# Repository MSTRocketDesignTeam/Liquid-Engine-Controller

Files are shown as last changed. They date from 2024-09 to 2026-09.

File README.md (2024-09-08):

<p align="center">
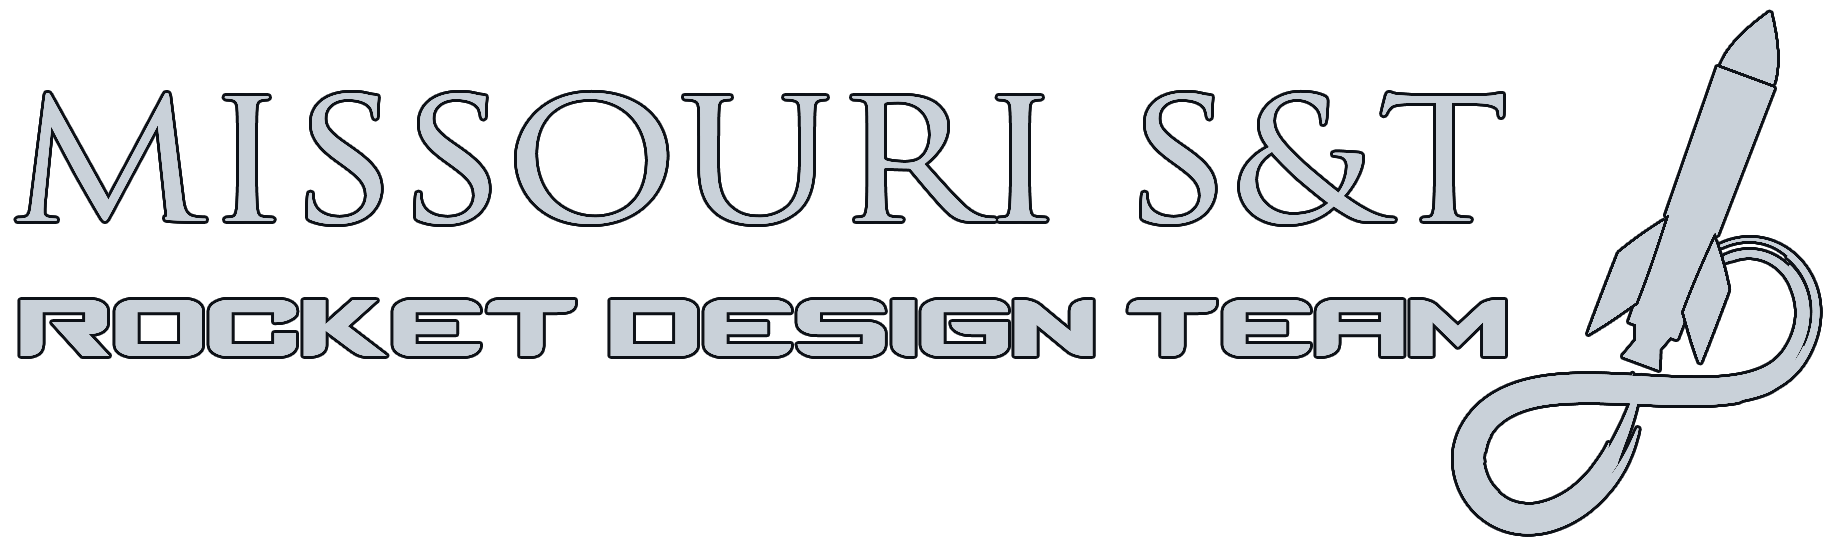
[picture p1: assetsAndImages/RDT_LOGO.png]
Missouri S&T Rocket Design Team
    
</p>

<p align="center"><sup><em>*This repo is intended for educational purposes only*</em></sup></p>

# SRAD Engine Controller
A student researched and designed (SRAD) engine controller for the liquid bipropellant rocket. 

## About
This project is the first iteration of the flight controller for the Rocket Design Team's (RDT) liquid bipropellant rocket.
It aims to provide basic engine control functionality, such as opening and closing of the servo ball valves (SBV), as well as to set the hardware baseline for more advanced control functionality like throttling algorithms for flight efficiency. Additionally, the Liquid Engine Controller (LEC) aims to serve as the data acquisition computer for the propulsion system, in order to analyze the performance of the propulsion system. 

## Documentation
*placeholder*

## Development 
*placeholder* 

## File Structure
This repo contains three main sections, hardware, firmware, and software.

### Hardware:
The hardware directory will contain all of the files related to the design and assembly of the PCBs. This includes KiCad projects as well as BOMs. 

### Firmware:
The firmware directory will contain all of the code (C++) necessary to operate the above hardware. Once the boards have been designed and assembled this is where significant effort will be made.

### Software: 
The software directory will contain the code (Python) for the LEC's computer interface. This program will be responsible for configuring the LEC prior to launch as well as for displaying live propulsion system state data from the launch pad. 

Future developments may allow for preflight simulations (FEA / CFD of engine, estimated throttling curve, etc.).

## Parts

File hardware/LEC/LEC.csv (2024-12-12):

Source: | C:\Users\Raksh\OneDrive\Desktop\Rocket_Repos\LEC\LEC_Attempts\Liquid-Engine-Controller\hardware\LEC\LEC.kicad_sch
Date: | 12/12/2024 8:57:48 AM
Tool: | Eeschema 7.0.8
Generator: | C:\Program Files\KiCad\7.0\bin\scripting\plugins/bom_csv_grouped_by_value.py
Component Count: | 66
Collated Components:
Item | Qty | Reference(s) | Value | LibPart | Footprint | Datasheet | DNP | DigiKey | MANUFACTURER | MAXIMUM_PACKAGE_HEIGHT | PARTREV | STANDARD
1 | 11 | C1, C2, C4, C5, C6, C7, C8, C9, C15, C16, C17 | 100n | Device:C | Capacitor_SMD:C_1206_3216Metric | ~ |  | https://www.digikey.com/en/products/detail/murata-electronics/GRM3195C1H104JA05D/13531811
2 | 3 | C3, C10, C11 | 100n | Device:C | Capacitor_SMD:C_0603_1608Metric | https://mm.digikey.com/Volume0/opasdata/d220001/medias/docus/609/CL10B104KB8NNNC_Spec.pdf |  | https://www.digikey.com/en/products/detail/samsung-electro-mechanics/CL10B104KB8NNNC/3886658
3 | 10 | C12, C13, C14, C18, C19, C20, C21, C22, C24, C25 | 10u | Device:C | Capacitor_SMD:C_0805_2012Metric | https://mm.digikey.com/Volume0/opasdata/d220001/medias/docus/5545/CL21A106KAYNNNE%20Spec.pdf |  | https://www.digikey.com/en/products/detail/samsung-electro-mechanics/CL21A106KAYNNNE/3888549
4 | 2 | C23, C26 | 10n | Device:C | Capacitor_SMD:C_0603_1608Metric | https://search.murata.co.jp/Ceramy/image/img/A01X/G101/ENG/GRM1885C1H103JA01-01.pdf |  | https://www.digikey.com/en/products/detail/murata-electronics/GRM1885C1H103JA01D/4421555
5 | 1 | D1 | 1N5817 | Diode:1N5817 | Diode_THT:D_DO-41_SOD81_P10.16mm_Horizontal | http://www.vishay.com/docs/88525/1n5817.pdf |  | https://www.digikey.com/en/products/detail/vishay-general-semiconductor-diodes-division/1N5817-E3-73/2139978
6 | 12 | J1, J2, J3, J4, J5, J6, J7, J8, J11, J12, J13, J14 | 54-00278 | 4_Pin_M8_Socket_Female:54-00278 | M8Connector:TENSILITY_54-00278 | https://tensility.s3.us-west-2.amazonaws.com/uploads/pdffiles/54-00278.pdf |  | https://www.digikey.com/en/products/detail/tensility-international-corp/54-00278/16604875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 | Tensility | 20.2 mm | A | Manufacturer Recommendations
7 | 2 | J9, J10 | Conn_01x02 | Connector_Generic:Conn_01x02 | Connector_AMASS:AMASS_XT30UPB-M_1x02_P5.0mm_Vertical | ~
8 | 16 | R1, R2, R3, R4, R5, R6, R7, R8, R9, R10, R11, R12, R13, R14, R15, R16 | 10K | Device:R_US | Resistor_SMD:R_0603_1608Metric | ~ |  | https://www.digikey.com/en/products/detail/vishay-dale/TNPW060310K0BEEA/1606881
9 | 1 | U1 | Pico | RaspberryPiPico:Pico | RPiPico:RPi_Pico_SMD_TH | https://datasheets.raspberrypi.com/pico/pico-datasheet.pdf |  | https://www.digikey.com/en/products/detail/raspberry-pi/SC0917/16608257
10 | 1 | U2 | L7805 | Regulator_Linear:L7805 | L7805CV:TO-220_STM | http://www.st.com/content/ccc/resource/technical/document/datasheet/41/4f/b3/b0/12/d4/47/88/CD00000444.pdf/files/CD00000444.pdf/jcr:content/translations/en.CD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 |  | https://www.digikey.com/en/products/detail/stmicroelectronics/L7805CV/585964
11 | 1 | U3 | MC7809CTG | MC7809CTG:MC7809CTG | MC7809CTG:TO-220AB_ONS | MC7809CTG |  | https://www.digikey.com/en/products/detail/onsemi/MC7809CTG/1481254
12 | 1 | U4 | W25Q128JVSIQ | W25Q128JVSIQ:W25Q128JVSIQ | W25Q128JVSIQ:SOIC_128JVSIQ_WIN | https://www.winbond.com/resource-files/W25Q128JV%20RevI%2008232021%20Plus.pdf |  | https://www.digikey.com/en/products/detail/winbond-electronics/W25Q128JVSIQ/5803943
13 | 2 | U5, U6 | MAX31855KASA | Sensor_Temperature:MAX31855KASA | Package_SO:SOIC-8_3.9x4.9mm_P1.27mm | http://datasheets.maximintegrated.com/en/ds/MAX31855.pdf |  | https://www.digikey.com/en/products/detail/analog-devices-inc-maxim-integrated/MAX31855KASA/2591564
14 | 2 | U7, U8 | L78L33ACZ | L78L33ACZ:L78L33ACZ | L78L33ACZ:TO-92-TR_STM | L78L33ACZ |  | https://www.digikey.com/en/products/detail/stmicroelectronics/L78L33ACZ/1038304
15 | 1 | U15 | MCP3564RT-E/ST | MCP3564:MCP3564RT-E_ST | MCP3564R/T:TSSOP20_ST_MCH | https://ww1.microchip.com/downloads/aemDocuments/documents/APID/ProductDocuments/DataSheets/MCP3561_2_4R-Data-Sheet-DS200006391C.pdf |  | https://www.digikey.com/en/products/detail/microchip-technology/MCP3564RT-E-ST/12807301

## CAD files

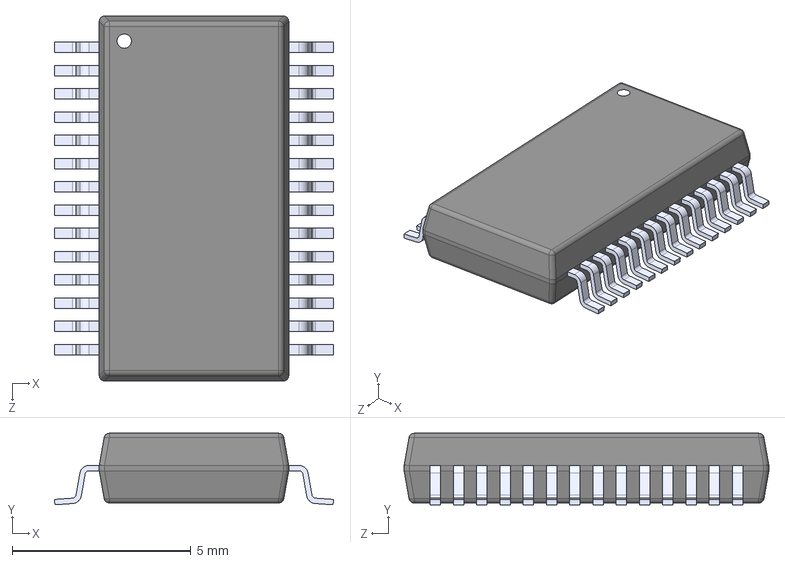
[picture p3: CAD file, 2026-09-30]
hardware/ADC Hat - LEC/components/ADS1256IDBR/ADS1256IDBR.step
7.80 x 2.00 x 10.2 mm

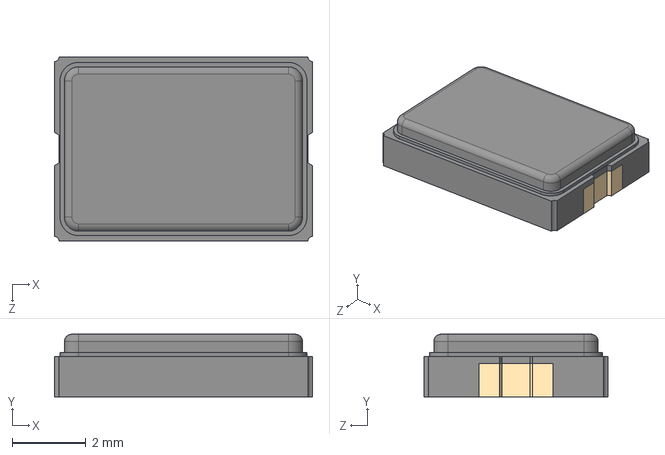
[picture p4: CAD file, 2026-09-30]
hardware/ADC Hat - LEC/components/ECS-100-S-20A-TR/ECS-100-S-20A-TR.step
7.00 x 1.70 x 5.00 mm

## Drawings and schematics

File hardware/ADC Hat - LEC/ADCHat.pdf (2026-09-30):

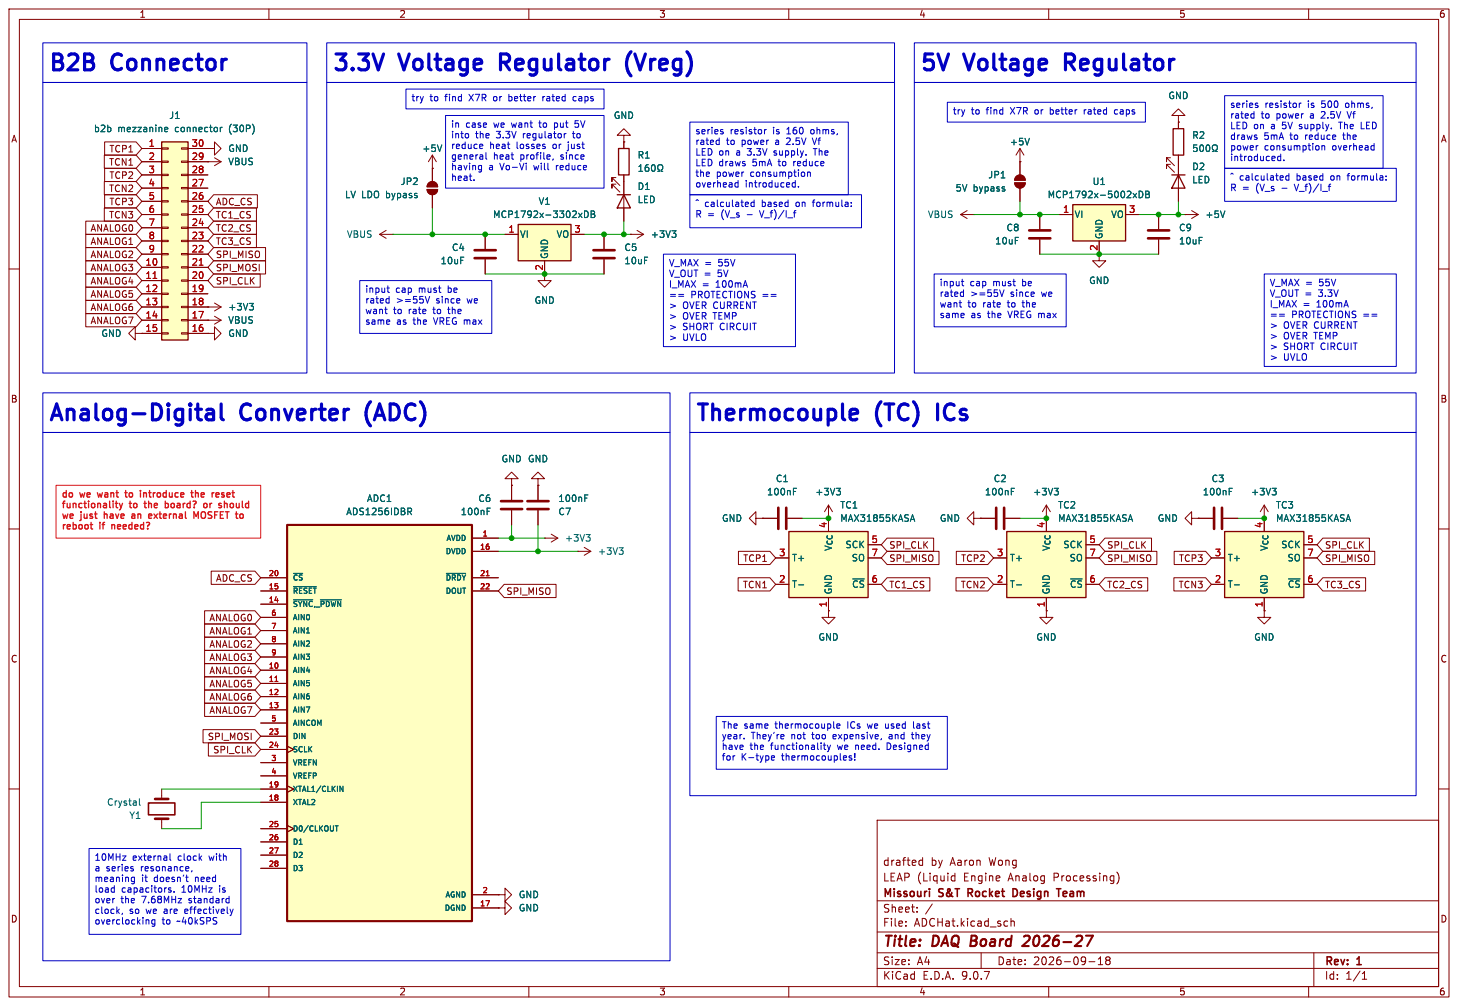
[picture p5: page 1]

https://www.digikey.com/en/products/filter/led-indication-discrete/105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 C6

try to find X7R or better rated caps Thermocouple (TC) ICs

in case we want to put 5V
reduce heat losses or just
having a Vo-Vi will reduce
heat.

draws 5mA to reduce the

LED draws 5mA to reduce
the power consumption
overhead introduced.

input cap must be

same as the VREG max

do we want to introduce the reset

1 SCK 5 SO 7 ~{CS}6 TC3 MAX31855KASA GND GND

1 SCK 5 SO 7 ~{CS}6 GND

1 SCK 5 SO 7 ~{CS}6 GND GND

a series resonance, meaning it doesn't need

clock, so we are effectively

Id: 1/1 Title: DAQ Board 2026-27

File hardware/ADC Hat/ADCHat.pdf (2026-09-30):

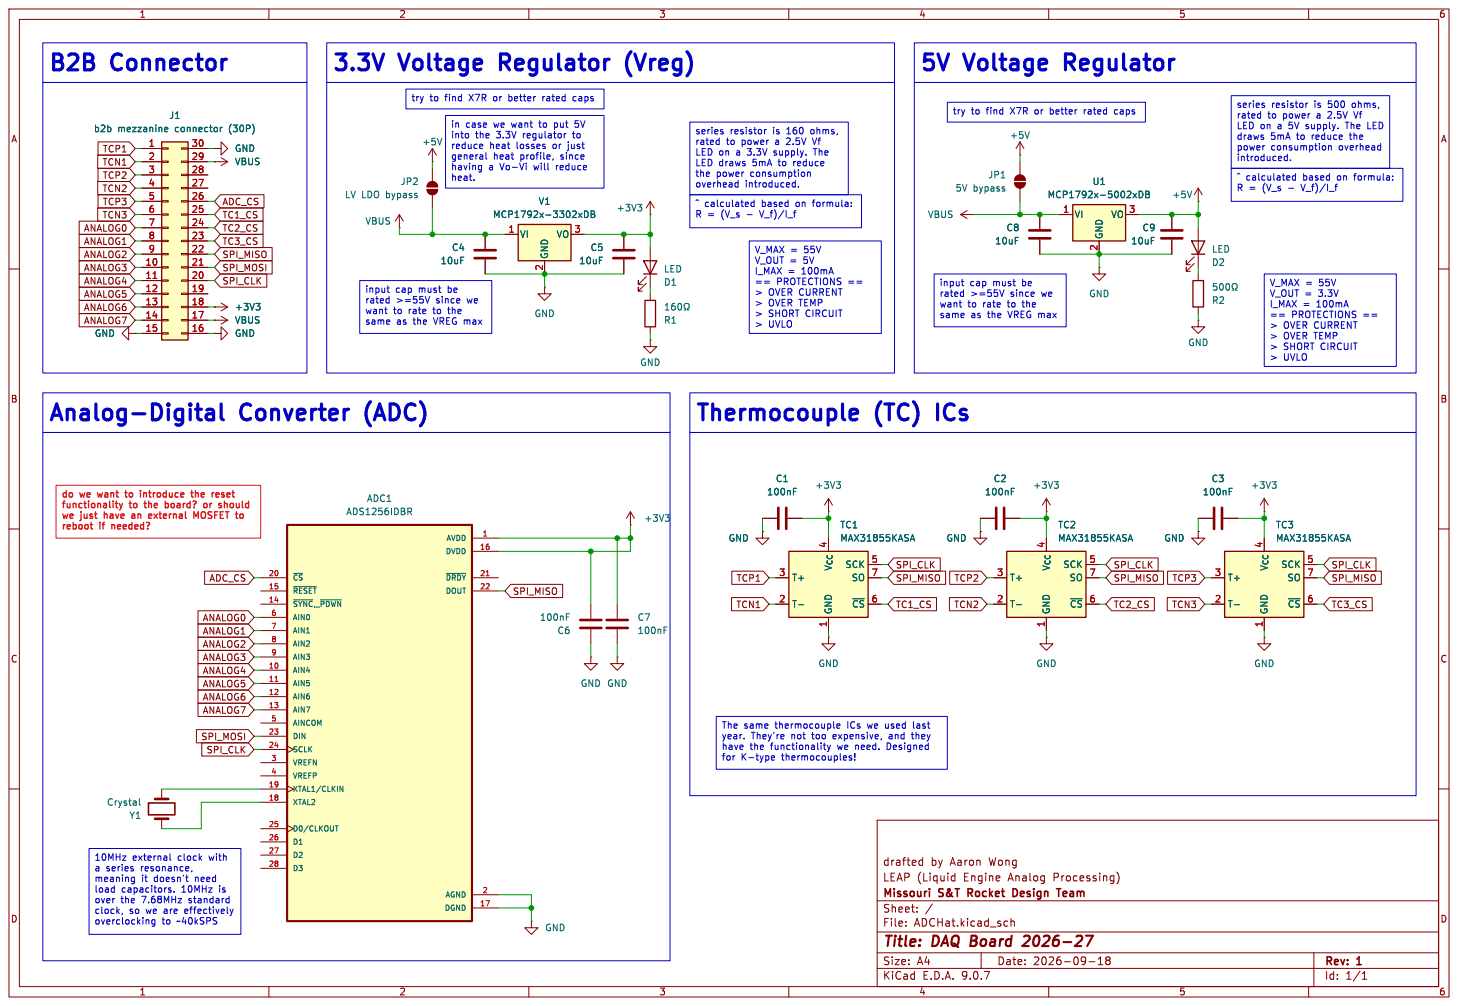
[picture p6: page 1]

https://www.digikey.com/en/products/filter/led-indication-discrete/105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 U1 MCP1792x-5002xDB

same as the VREG max 5V Voltage Regulator

try to find X7R or better rated caps

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

LED draws 5mA to reduce
the power consumption
overhead introduced. Thermocouple (TC) ICs

LV LDO bypass VBUS

input cap must be

1 SCK 5 SO 7 ~{CS}6 TC1 GND MAX31855KASA C1
100nF GND

1 SCK 5 SO 7 ~{CS}6 TC2 MAX31855KASA GND GND

a series resonance, meaning it doesn't need

clock, so we are effectively

Id: 1/1 Title: DAQ Board 2026-27

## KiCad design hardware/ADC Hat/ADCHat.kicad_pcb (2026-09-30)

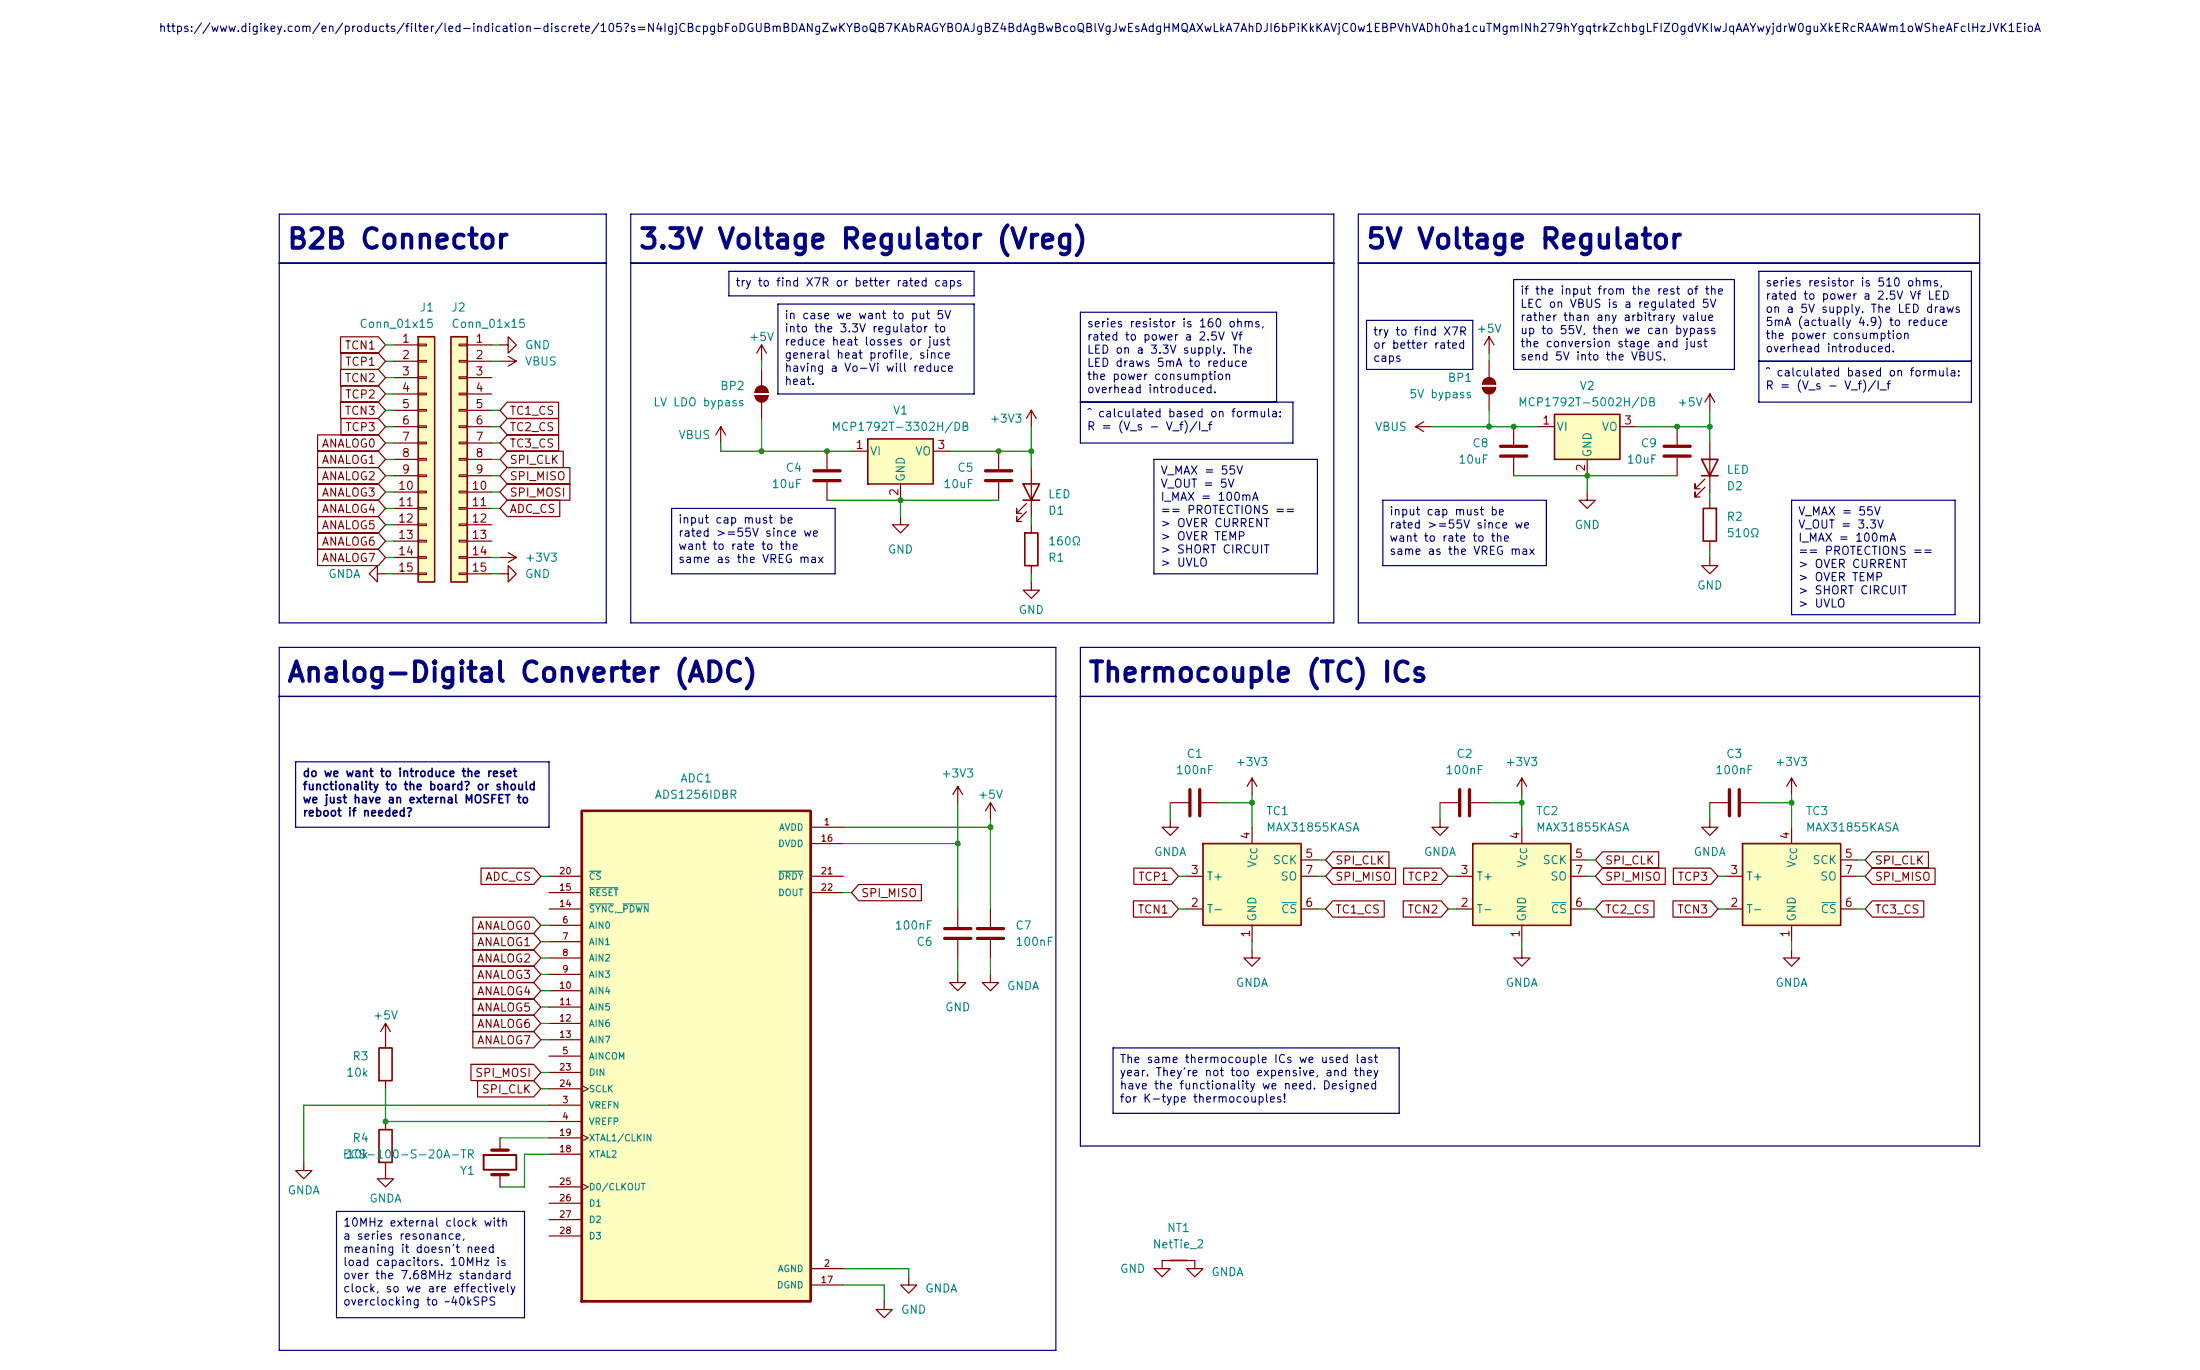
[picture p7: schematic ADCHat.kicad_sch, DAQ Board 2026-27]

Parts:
ADC1: ADS1256IDBR; SOP65P780X200-28N; DIGIKEY_ID ADS1256IDBR
BP1: 5V bypass; SolderJumper-2_P1.3mm_Open_RoundedPad1.0x1.5mm
BP2: LV LDO bypass; SolderJumper-2_P1.3mm_Open_RoundedPad1.0x1.5mm
C1, C2, C3: 100nF; C_0402_1005Metric; DIGIKEY_ID GRM155R71H104KE14D
C4, C8: 10uF; C_0805_2012Metric; DIGIKEY_ID GMC21X5R106K50NT
C5, C9: 10uF; C_0805_2012Metric; DIGIKEY_ID CL21A106KPFNNNG
C6, C7: 100nF; C_0805_2012Metric; DIGIKEY_ID CL21B104KBCNNNC
D1, D2: LED; LED_0603_1608Metric; DIGIKEY_ID KT EELP41.12-S2U1-25-2X4Y-5-R18
J1, J2: Conn_01x15; PinHeader_1x15_P2.54mm_Vertical
NT1: NetTie_2; NetTie-2_SMD_Pad0.5mm
R1: 160Ω; R_0603_1608Metric; DIGIKEY_ID RC0402FR-07160RL
R2: 510Ω; R_0603_1608Metric; DIGIKEY_ID RC0402FR-07510RL
R3, R4: 10k; R_0603_1608Metric; DIGIKEY_ID RNCF0402BTE10K0
TC1, TC2, TC3: MAX31855KASA; SOIC-8_3.9x4.9mm_P1.27mm; DIGIKEY_ID MAX31855KASA+T
V1: MCP1792T-3302H/DB; SOT-223-3_TabPin2; DIGIKEY_ID MCP1792T-3302H/DB
V2: MCP1792T-5002H/DB; SOT-223-3_TabPin2; DIGIKEY_ID MCP1792T-5002H/DB
Y1: ECS-100-S-20A-TR; XTAL_ECS-100-S-20A-TR; DIGIKEY_ID ECS-100-S-20A-TR

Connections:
+3V3: ADC1.16 (DVDD), C1.2, C2.2, C3.2, C5.1, C6.1, D1.2 (A), J2.14, TC1.4 (V_{CC}), TC2.4 (V_{CC}), TC3.4 (V_{CC}), V1.3 (VO)
+5V: ADC1.1 (AVDD), BP1.2 (B), BP2.2 (B), C7.2, C9.1, D2.2 (A), R3.1, V2.3 (VO)
ADC_CS: ADC1.20 (~CS), J2.11
ANALOG0: ADC1.6 (AIN0), J1.7
ANALOG1: ADC1.7 (AIN1), J1.8
ANALOG2: ADC1.8 (AIN2), J1.9
ANALOG3: ADC1.9 (AIN3), J1.10
ANALOG4: ADC1.10 (AIN4), J1.11
ANALOG5: ADC1.11 (AIN5), J1.12
ANALOG6: ADC1.12 (AIN6), J1.13
ANALOG7: ADC1.13 (AIN7), J1.14
GND: ADC1.17 (DGND), C4.2, C5.2, C6.2, C8.2, C9.2, J2.1, J2.15, NT1.1, R1.1, R2.1, V1.2 (GND), V2.2 (GND)
GNDA: ADC1.2 (AGND), ADC1.3 (VREFN), C1.1, C2.1, C3.1, C7.1, J1.15, NT1.2, R4.2, TC1.1 (GND), TC2.1 (GND), TC3.1 (GND)
unnamed: ADC1.4 (VREFP), R3.2, R4.1
unnamed: ADC1.19 (XTAL1/CLKIN), Y1.1
unnamed: ADC1.18 (XTAL2), Y1.2
unnamed: D1.1 (K), R1.2
unnamed: D2.1 (K), R2.2
SPI_CLK: ADC1.24 (SCLK), J2.8, TC1.5 (SCK), TC2.5 (SCK), TC3.5 (SCK)
SPI_MISO: ADC1.22 (DOUT), J2.9, TC1.7 (SO), TC2.7 (SO), TC3.7 (SO)
SPI_MOSI: ADC1.23 (DIN), J2.10
TC1_CS: J2.5, TC1.6 (~CS)
TC2_CS: J2.6, TC2.6 (~CS)
TC3_CS: J2.7, TC3.6 (~CS)
TCN1: J1.1, TC1.2 (T-)
TCN2: J1.3, TC2.2 (T-)
TCN3: J1.5, TC3.2 (T-)
TCP1: J1.2, TC1.3 (T+)
TCP2: J1.4, TC2.3 (T+)
TCP3: J1.6, TC3.3 (T+)
VBUS: BP1.1 (A), BP2.1 (A), C4.1, C8.1, J2.2, V1.1 (VI), V2.1 (VI)

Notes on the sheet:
https://www.digikey.com/en/products/filter/led-indication-discrete/105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
10MHz external clock with a series resonance, meaning it doesn't need load capacitors. 10MHz is over the 7.68MHz standard clock, so we are effectively overclocking to ~40kSPS
in case we want to put 5V into the 3.3V regulator to reduce heat losses or just general heat profile, since having a Vo-Vi will reduce heat.
input cap must be rated >=55V since we want to rate to the same as the VREG max
5V Voltage Regulator
try to find X7R or better rated caps
V_MAX = 55V V_OUT = 5V I_MAX = 100mA == PROTECTIONS == > OVER CURRENT > OVER TEMP > SHORT CIRCUIT > UVLO
^ calculated based on formula: R = (V_s - V_f)/I_f
do we want to introduce the reset functionality to the board? or should we just have an external MOSFET to reboot if needed?
if the input from the rest of the LEC on VBUS is a regulated 5V rather than any arbitrary value up to 55V, then we can bypass the conversion stage and just send 5V into the VBUS.
Analog-Digital Converter (ADC)
The same thermocouple ICs we used last year. They're not too expensive, and they have the functionality we need. Designed for K-type thermocouples!
3.3V Voltage Regulator (Vreg)
V_MAX = 55V V_OUT = 3.3V I_MAX = 100mA == PROTECTIONS == > OVER CURRENT > OVER TEMP > SHORT CIRCUIT > UVLO
series resistor is 160 ohms, rated to power a 2.5V Vf LED on a 3.3V supply. The LED draws 5mA to reduce the power consumption overhead introduced.
series resistor is 510 ohms, rated to power a 2.5V Vf LED on a 5V supply. The LED draws 5mA (actually 4.9) to reduce the power consumption overhead introduced.
Thermocouple (TC) ICs
B2B Connector

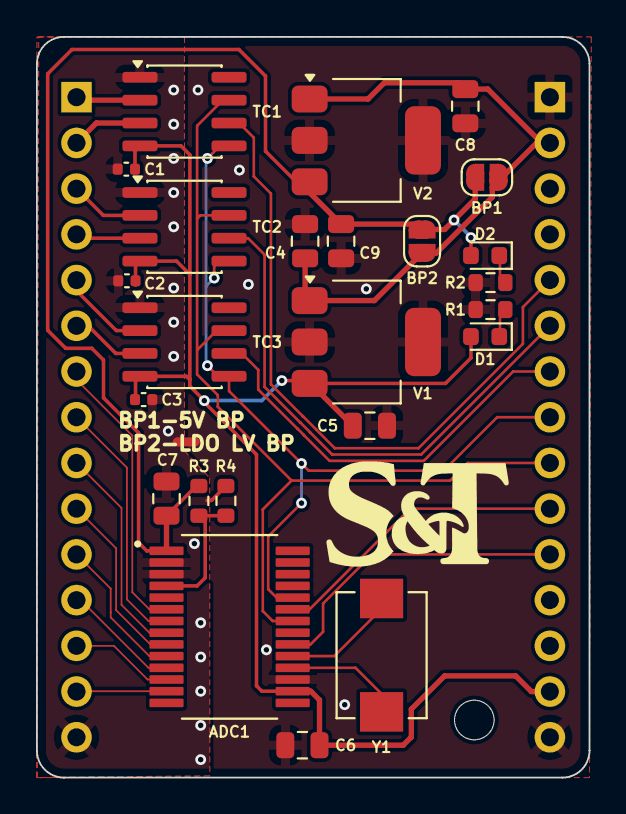
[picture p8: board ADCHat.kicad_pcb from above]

Board: 2 copper layers, 30.7 x 41.1 mm, 27 parts (0 on the bottom side), 31 nets.

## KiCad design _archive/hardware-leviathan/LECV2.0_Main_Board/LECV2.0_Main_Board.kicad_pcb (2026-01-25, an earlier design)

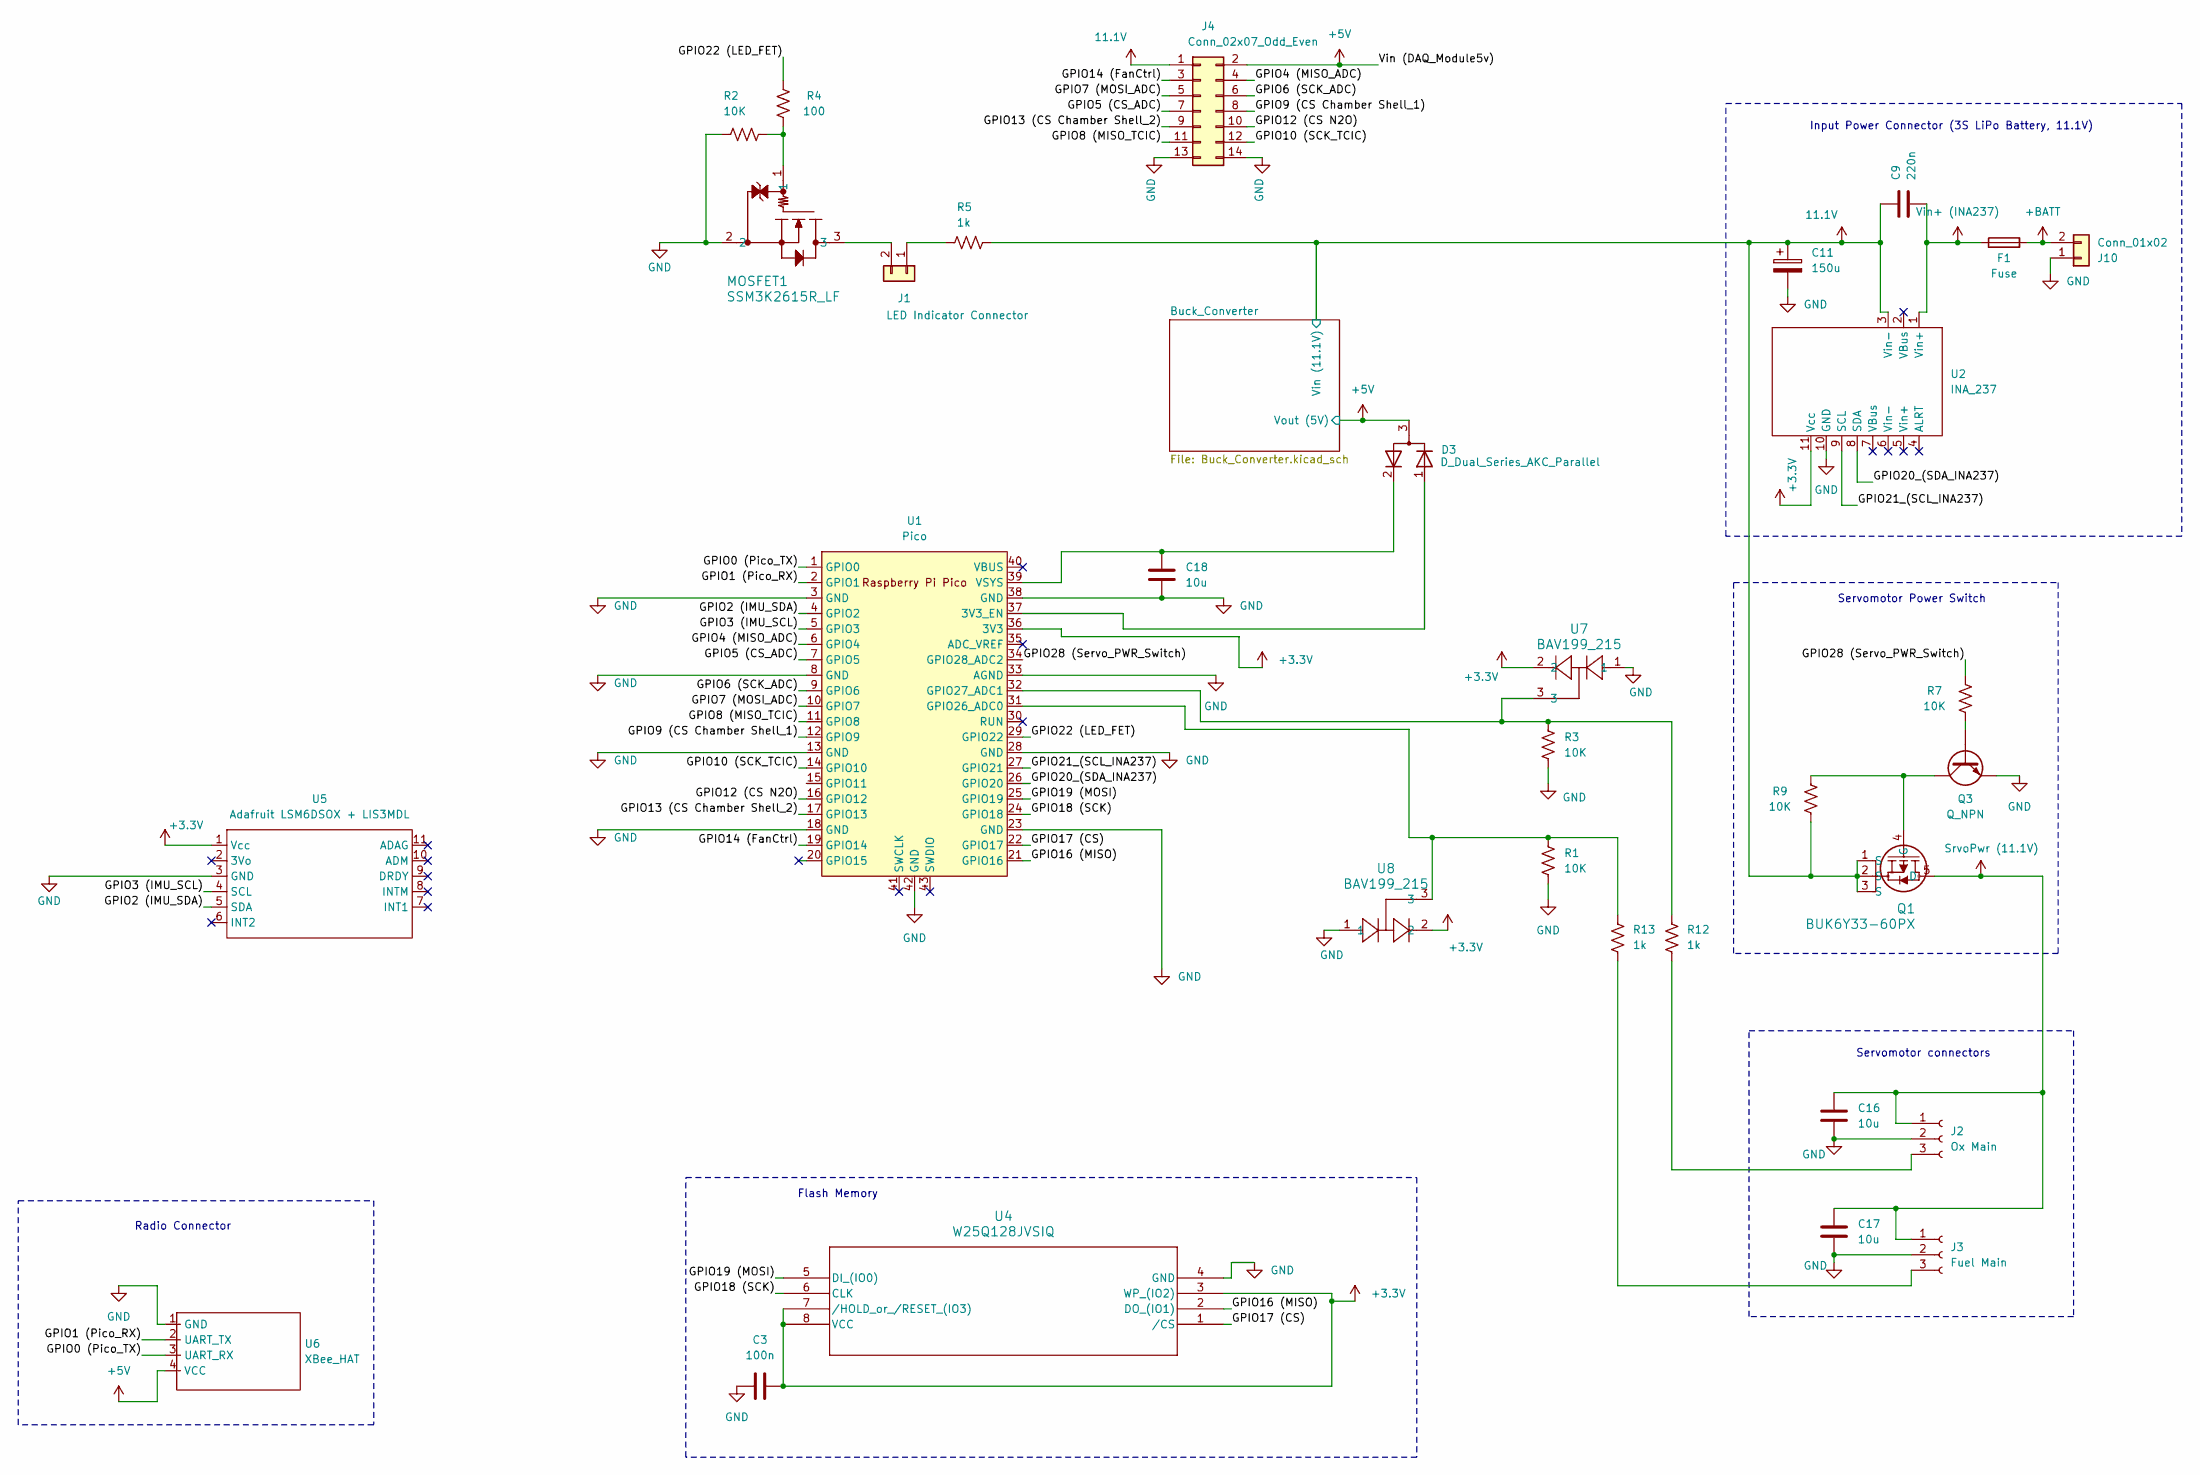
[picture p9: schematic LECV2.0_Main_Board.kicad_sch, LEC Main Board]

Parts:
C3: 100n; C_0603_1608Metric
C9: 220n; C_0805_2012Metric
C11: 150u; CAPPRD500W60D1000H1600
C16, C17, C18: 10u; C_1210_3225Metric
D3: D_Dual_Series_AKC_Parallel; SOT-23
F1: Fuse; Fuse_1206_3216Metric
J1: LED Indicator Connector; PinHeader_1x02_P2.54mm_Vertical
J2: Ox Main; TENSILITY_54-00440
J3: Fuel Main; TENSILITY_54-00440
J4: Conn_02x07_Odd_Even; PinHeader_2x07_P2.54mm_Vertical
J10: Conn_01x02; AMASS_XT30UPB-M_1x02_P5.0mm_Vertical
MOSFET1: SSM3K2615R_LF; SOT-23F_TOS
Q1: BUK6Y33-60PX; LFPAK_SOT669_NEX
Q3: Q_NPN; SOT-323_SC-70
R1, R2, R3, R7, R9: 10K; R_0603_1608Metric
R4: 100; R_0603_1608Metric
R5, R12, R13: 1k; R_0603_1608Metric
U1: Pico; RPi_Pico_SMD_TH
U2: INA_237; INA238_MODULE
U4: W25Q128JVSIQ; SOIC_128JVSIQ_WIN
U5: Adafruit LSM6DSOX + LIS3MDL; Adafruit_LSM6DSOX+LIS3MDL
U6: XBee_HAT; XBee-HAT
U7, U8: BAV199_215; SOT-23-3

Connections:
11.1V: C9.1, C11.1, J4.1, Q1.1 (S), Q1.2 (S), Q1.3 (S), R5.2, R9.1, U2.3 (Vin-); also elsewhere on the board
+3.3V: C3.2, U1.36 (3V3), U2.11 (Vcc), U4.3 (WP_(IO2)), U4.7 (/HOLD_or_/RESET_(IO3)), U4.8 (VCC), U5.1 (Vcc), U7.2, U8.2
+5V: D3.3 (common), J4.2, U6.4 (VCC); also elsewhere on the board
+BATT: F1.2, J10.2
/GPIO0 (Pico_TX): U1.1 (GPIO0), U6.3 (UART_RX)
/GPIO1 (Pico_RX): U1.2 (GPIO1), U6.2 (UART_TX)
/GPIO2 (IMU_SDA): U1.4 (GPIO2), U5.5 (SDA)
/GPIO3 (IMU_SCL): U1.5 (GPIO3), U5.4 (SCL)
/GPIO4 (MISO_ADC): J4.4, U1.6 (GPIO4)
/GPIO5 (CS_ADC): J4.7, U1.7 (GPIO5)
/GPIO6 (SCK_ADC): J4.6, U1.9 (GPIO6)
/GPIO7 (MOSI_ADC): J4.5, U1.10 (GPIO7)
/GPIO8 (MISO_TCIC): J4.11, U1.11 (GPIO8)
/GPIO9 (CS Chamber Shell_1): J4.8, U1.12 (GPIO9)
/GPIO10 (SCK_TCIC): J4.12, U1.14 (GPIO10)
/GPIO12 (CS N2O): J4.10, U1.16 (GPIO12)
/GPIO13 (CS Chamber Shell_2): J4.9, U1.17 (GPIO13)
/GPIO14 (FanCtrl): J4.3, U1.19 (GPIO14)
/GPIO16 (MISO): U1.21 (GPIO16), U4.2 (DO_(IO1))
/GPIO17 (CS): U1.22 (GPIO17), U4.1 (/CS)
/GPIO18 (SCK): U1.24 (GPIO18), U4.6 (CLK)
/GPIO19 (MOSI): U1.25 (GPIO19), U4.5 (DI_(IO0))
/GPIO20_(SDA_INA237): U1.26 (GPIO20), U2.8 (SDA)
/GPIO21_(SCL_INA237): U1.27 (GPIO21), U2.9 (SCL)
/GPIO22 (LED_FET): R4.1, U1.29 (GPIO22)
/GPIO28 (Servo_PWR_Switch): R7.2, U1.34 (GPIO28_ADC2)
GND: C3.1, C11.2, C16.2, C17.2, C18.2, J2.2, J3.2, J4.13, J4.14, J10.1, MOSFET1.2, Q3.2 (E), R1.2, R2.2, R3.2, U1.3 (GND), U1.8 (GND), U1.13 (GND), U1.18 (GND), U1.23 (GND), U1.28 (GND), U1.33 (AGND), U1.38 (GND), U1.42 (GND), U2.10 (GND), U4.4 (GND), U5.3 (GND), U6.1 (GND), U7.1, U8.1; also elsewhere on the board
unnamed: D3.1 (A), U1.37 (3V3_EN)
unnamed: C18.1, D3.2 (K), U1.39 (VSYS)
unnamed: J1.1, R5.1
unnamed: J1.2, MOSFET1.3
unnamed: J2.3, R12.2
unnamed: J3.3, R13.2
unnamed: MOSFET1.1, R2.1, R4.2
unnamed: Q1.4 (G), Q3.3 (C), R9.2
unnamed: Q3.1 (B), R7.1
unnamed: R1.1, R13.1, U1.31 (GPIO26_ADC0), U8.3
unnamed: R3.1, R12.1, U1.32 (GPIO27_ADC1), U7.3
SrvoPwr (11.1V): C16.1, C17.1, J2.1, J3.1, Q1.5 (D)
Vin+ (INA237): C9.2, F1.1, U2.1 (Vin+)

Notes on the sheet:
Flash Memory
Radio Connector
Servomotor Power Switch
Input Power Connector (3S LiPo Battery, 11.1V)
Servomotor connectors

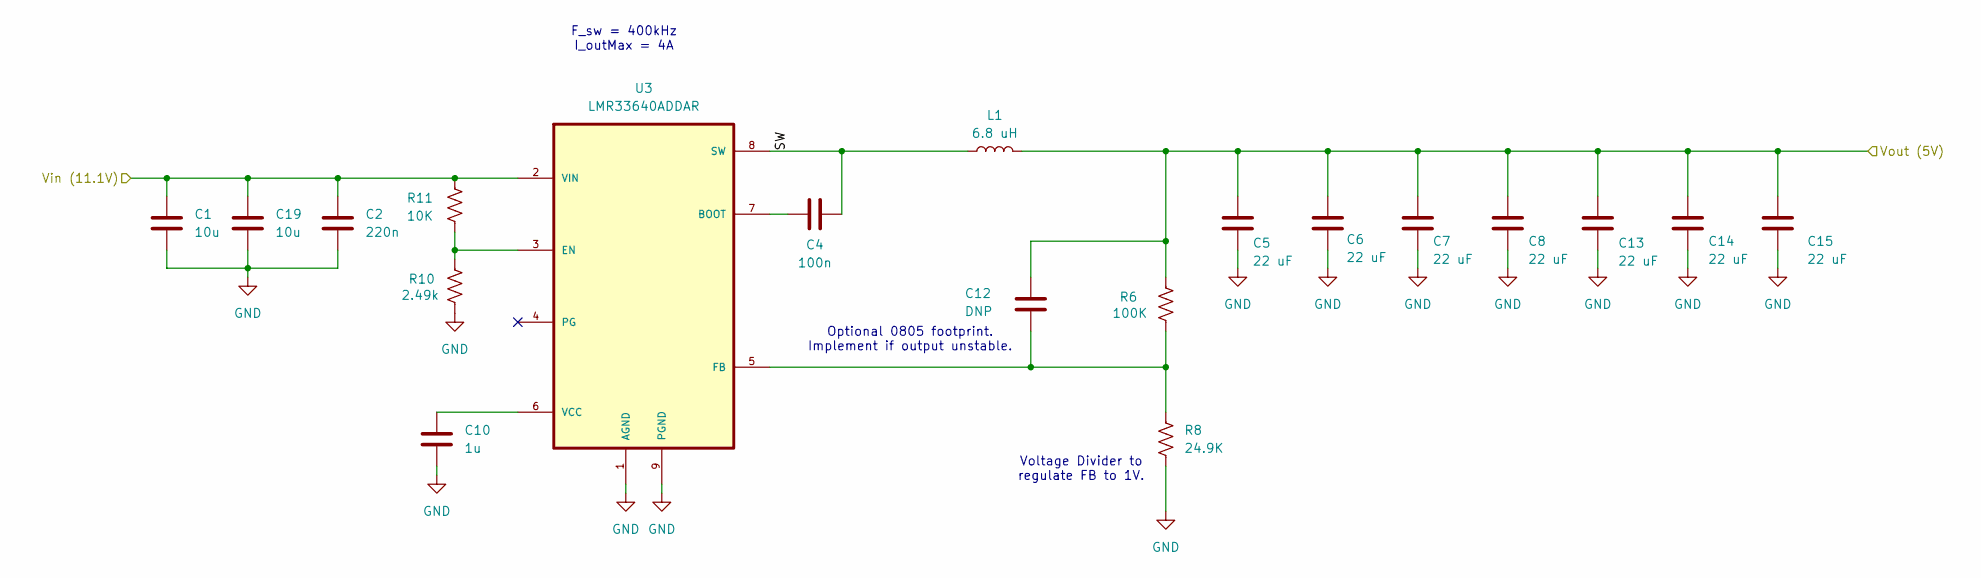
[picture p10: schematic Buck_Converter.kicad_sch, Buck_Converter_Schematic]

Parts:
C1, C19: 10u; C_1210_3225Metric
C2: 220n; C_0805_2012Metric
C4: 100n; C_0603_1608Metric
C5, C6, C7, C8, C13, C14, C15: 22 uF; C_0805_2012Metric
C10: 1u; C_0805_2012Metric
C12: DNP; C_0805_2012Metric
L1: 6.8 uH; IND_CSBX0650-6R8M
R6: 100K; R_0603_1608Metric
R8: 24.9K; R_0603_1608Metric
R10: 2.49k; R_0603_1608Metric
R11: 10K; R_0603_1608Metric
U3: LMR33640ADDAR; Texas_HSOP-8-1EP_3.9x4.9mm_P1.27mm_ThermalVias

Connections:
11.1V: C1.1, C2.1, C19.1, R11.1, U3.2 (VIN); also elsewhere on the board
+5V: C5.1, C6.1, C7.1, C8.1, C12.2, C13.1, C14.1, C15.1, L1.2, R6.2; also elsewhere on the board
/Buck_Converter/SW: C4.2, L1.1, U3.8 (SW)
GND: C1.2, C2.2, C5.2, C6.2, C7.2, C8.2, C10.2, C13.2, C14.2, C15.2, C19.2, R8.2, R10.1, U3.1 (AGND), U3.9 (PGND); also elsewhere on the board
unnamed: C4.1, U3.7 (BOOT)
unnamed: R10.2, R11.2, U3.3 (EN)
unnamed: C12.1, R6.1, R8.1, U3.5 (FB)
unnamed: C10.1, U3.6 (VCC)

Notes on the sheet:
Optional 0805 footprint. Implement if output unstable.
Voltage Divider to regulate FB to 1V.
F_sw = 400kHz I_outMax = 4A

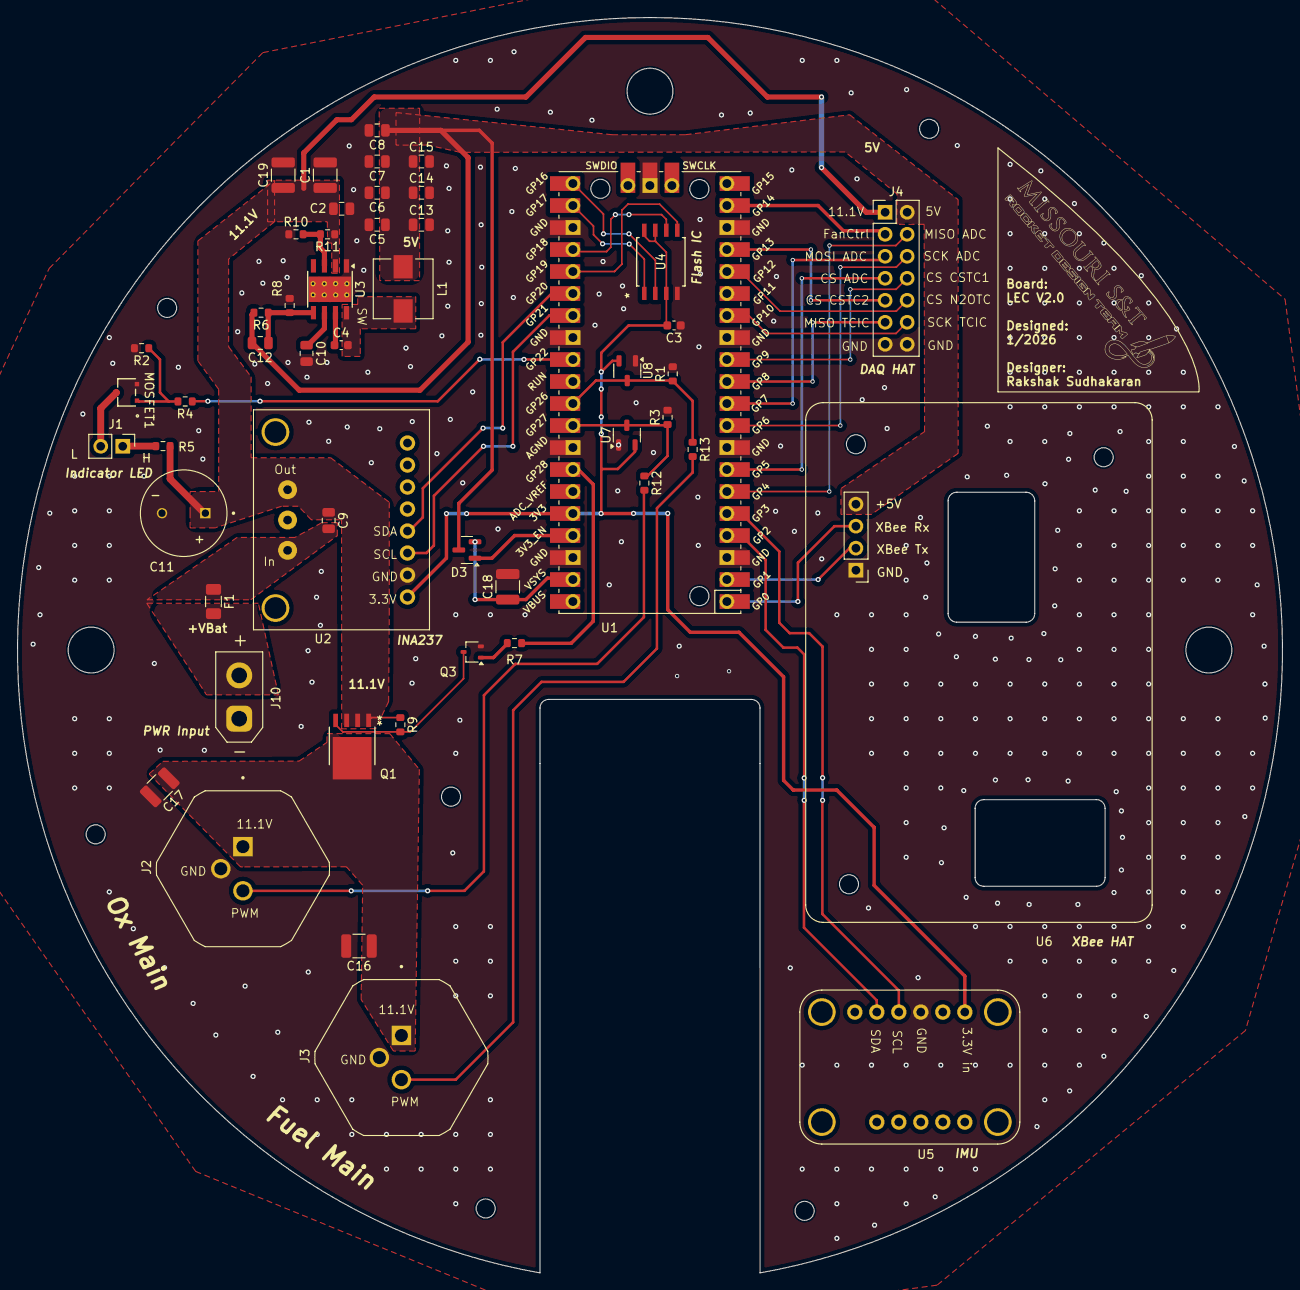
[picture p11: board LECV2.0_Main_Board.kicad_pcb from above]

Board: 2 copper layers, 146.0 x 144.9 mm, 51 parts (0 on the bottom side), 45 nets.

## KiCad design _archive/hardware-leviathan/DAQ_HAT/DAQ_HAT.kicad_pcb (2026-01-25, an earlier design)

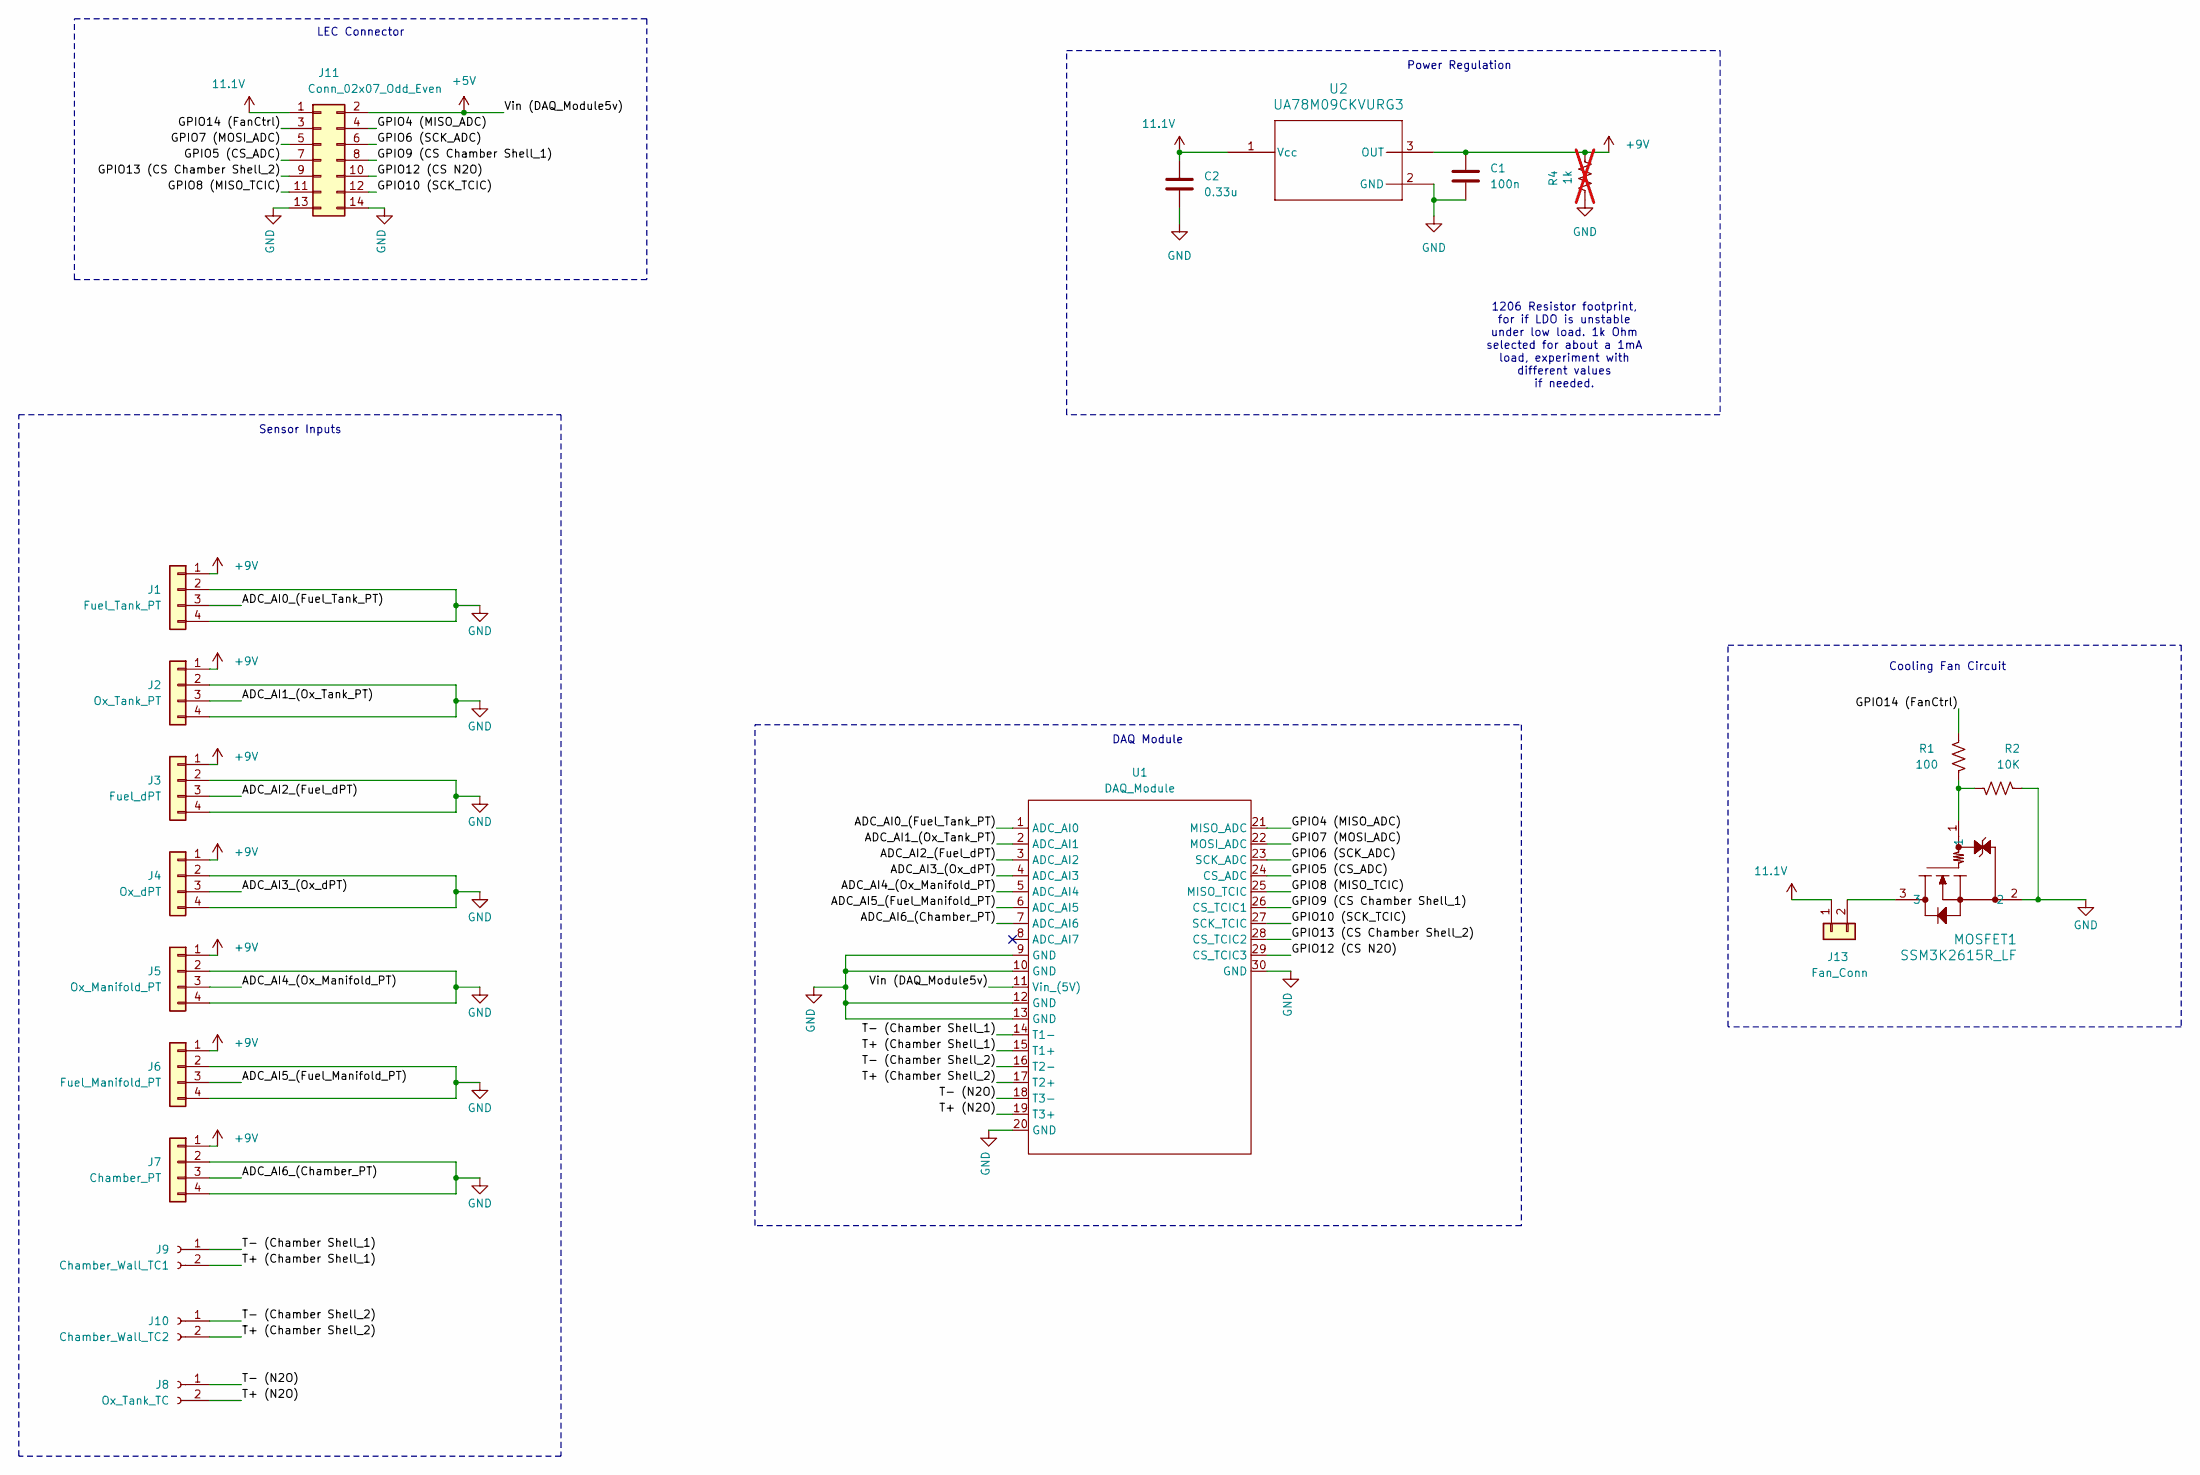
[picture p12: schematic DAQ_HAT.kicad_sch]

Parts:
C1: 100n; C_0603_1608Metric
C2: 0.33u; C_1206_3216Metric
J1: Fuel_Tank_PT; TENSILITY_54-00278
J2: Ox_Tank_PT; TENSILITY_54-00278
J3: Fuel_dPT; TENSILITY_54-00278
J4: Ox_dPT; TENSILITY_54-00278
J5: Ox_Manifold_PT; TENSILITY_54-00278
J6: Fuel_Manifold_PT; TENSILITY_54-00278
J7: Chamber_PT; TENSILITY_54-00278
J8: Ox_Tank_TC; PinHeader_1x02_P2.54mm_Vertical
J9: Chamber_Wall_TC1; PinHeader_1x02_P2.54mm_Vertical
J10: Chamber_Wall_TC2; PinHeader_1x02_P2.54mm_Vertical
J11: Conn_02x07_Odd_Even; PinHeader_2x07_P2.54mm_Vertical
J13: Fan_Conn; PinHeader_1x02_P2.54mm_Vertical
MOSFET1: SSM3K2615R_LF; SOT-23F_TOS
R1: 100; R_0603_1608Metric
R2: 10K; R_0603_1608Metric
R4: 1k; R_1206_3216Metric; not fitted
U1: DAQ_Module
U2: UA78M09CKVURG3; TO-252-2

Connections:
11.1V: C2.2, J11.1, J13.1, U2.1 (Vcc)
+5V: J11.2, U1.11 (Vin_(5V))
+9V: C1.2, J1.1, J2.1, J3.1, J4.1, J5.1, J6.1, J7.1, R4.1, U2.3 (OUT)
/ADC_AI0_(Fuel_Tank_PT): J1.3, U1.1 (ADC_AI0)
/ADC_AI1_(Ox_Tank_PT): J2.3, U1.2 (ADC_AI1)
/ADC_AI2_(Fuel_dPT): J3.3, U1.3 (ADC_AI2)
/ADC_AI3_(Ox_dPT): J4.3, U1.4 (ADC_AI3)
/ADC_AI4_(Ox_Manifold_PT): J5.3, U1.5 (ADC_AI4)
/ADC_AI5_(Fuel_Manifold_PT): J6.3, U1.6 (ADC_AI5)
/ADC_AI6_(Chamber_PT): J7.3, U1.7 (ADC_AI6)
/GPIO4 (MISO_ADC): J11.4, U1.21 (MISO_ADC)
/GPIO5 (CS_ADC): J11.7, U1.24 (CS_ADC)
/GPIO6 (SCK_ADC): J11.6, U1.23 (SCK_ADC)
/GPIO7 (MOSI_ADC): J11.5, U1.22 (MOSI_ADC)
/GPIO8 (MISO_TCIC): J11.11, U1.25 (MISO_TCIC)
/GPIO9 (CS Chamber Shell_1): J11.8, U1.26 (CS_TCIC1)
/GPIO10 (SCK_TCIC): J11.12, U1.27 (SCK_TCIC)
/GPIO12 (CS N2O): J11.10, U1.29 (CS_TCIC3)
/GPIO13 (CS Chamber Shell_2): J11.9, U1.28 (CS_TCIC2)
/GPIO14 (FanCtrl): J11.3, R1.1
/T+ (Chamber Shell_1): J9.2, U1.15 (T1+)
/T+ (Chamber Shell_2): J10.2, U1.17 (T2+)
/T+ (N2O): J8.2, U1.19 (T3+)
/T- (Chamber Shell_1): J9.1, U1.14 (T1-)
/T- (Chamber Shell_2): J10.1, U1.16 (T2-)
/T- (N2O): J8.1, U1.18 (T3-)
GND: C1.1, C2.1, J1.2, J1.4, J2.2, J2.4, J3.2, J3.4, J4.2, J4.4, J5.2, J5.4, J6.2, J6.4, J7.2, J7.4, J11.13, J11.14, MOSFET1.2, R2.2, R4.2, U1.9 (GND), U1.10 (GND), U1.12 (GND), U1.13 (GND), U1.20 (GND), U1.30 (GND), U2.2 (GND)
unnamed: J13.2, MOSFET1.3
unnamed: MOSFET1.1, R1.2, R2.1

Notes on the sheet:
Cooling Fan Circuit
LEC Connector
Sensor Inputs
Power Regulation
DAQ Module
1206 Resistor footprint, for if LDO is unstable under low load. 1k Ohm selected for about a 1mA load, experiment with different values if needed.

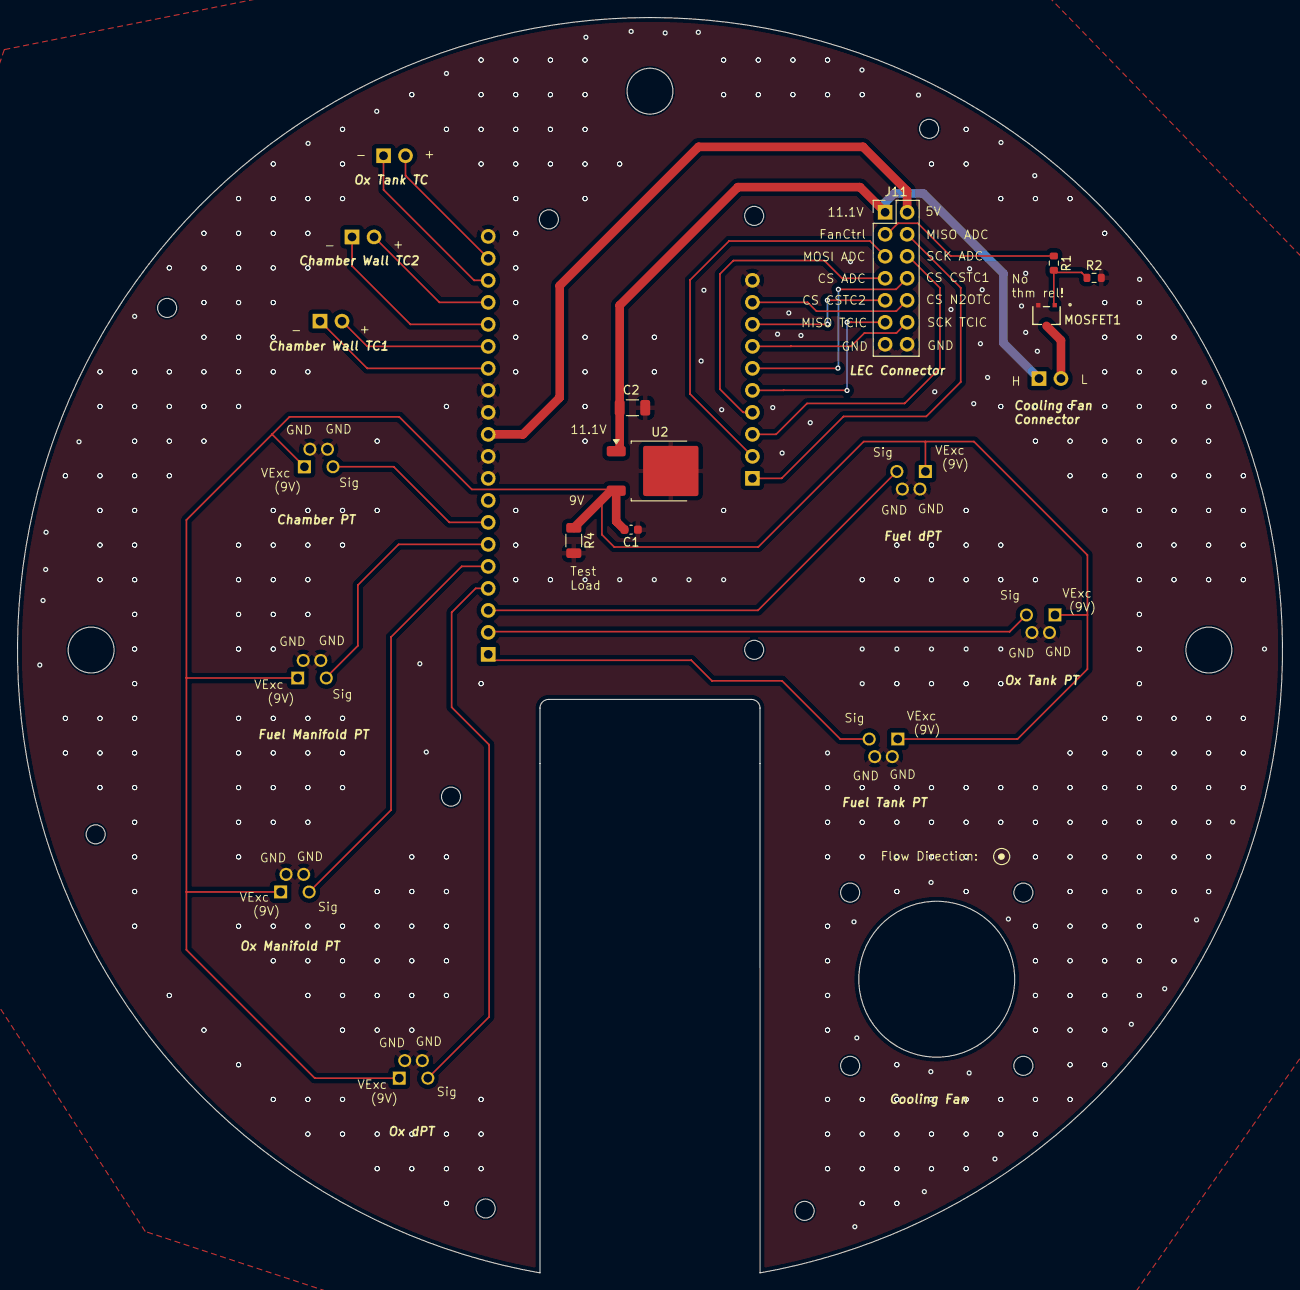
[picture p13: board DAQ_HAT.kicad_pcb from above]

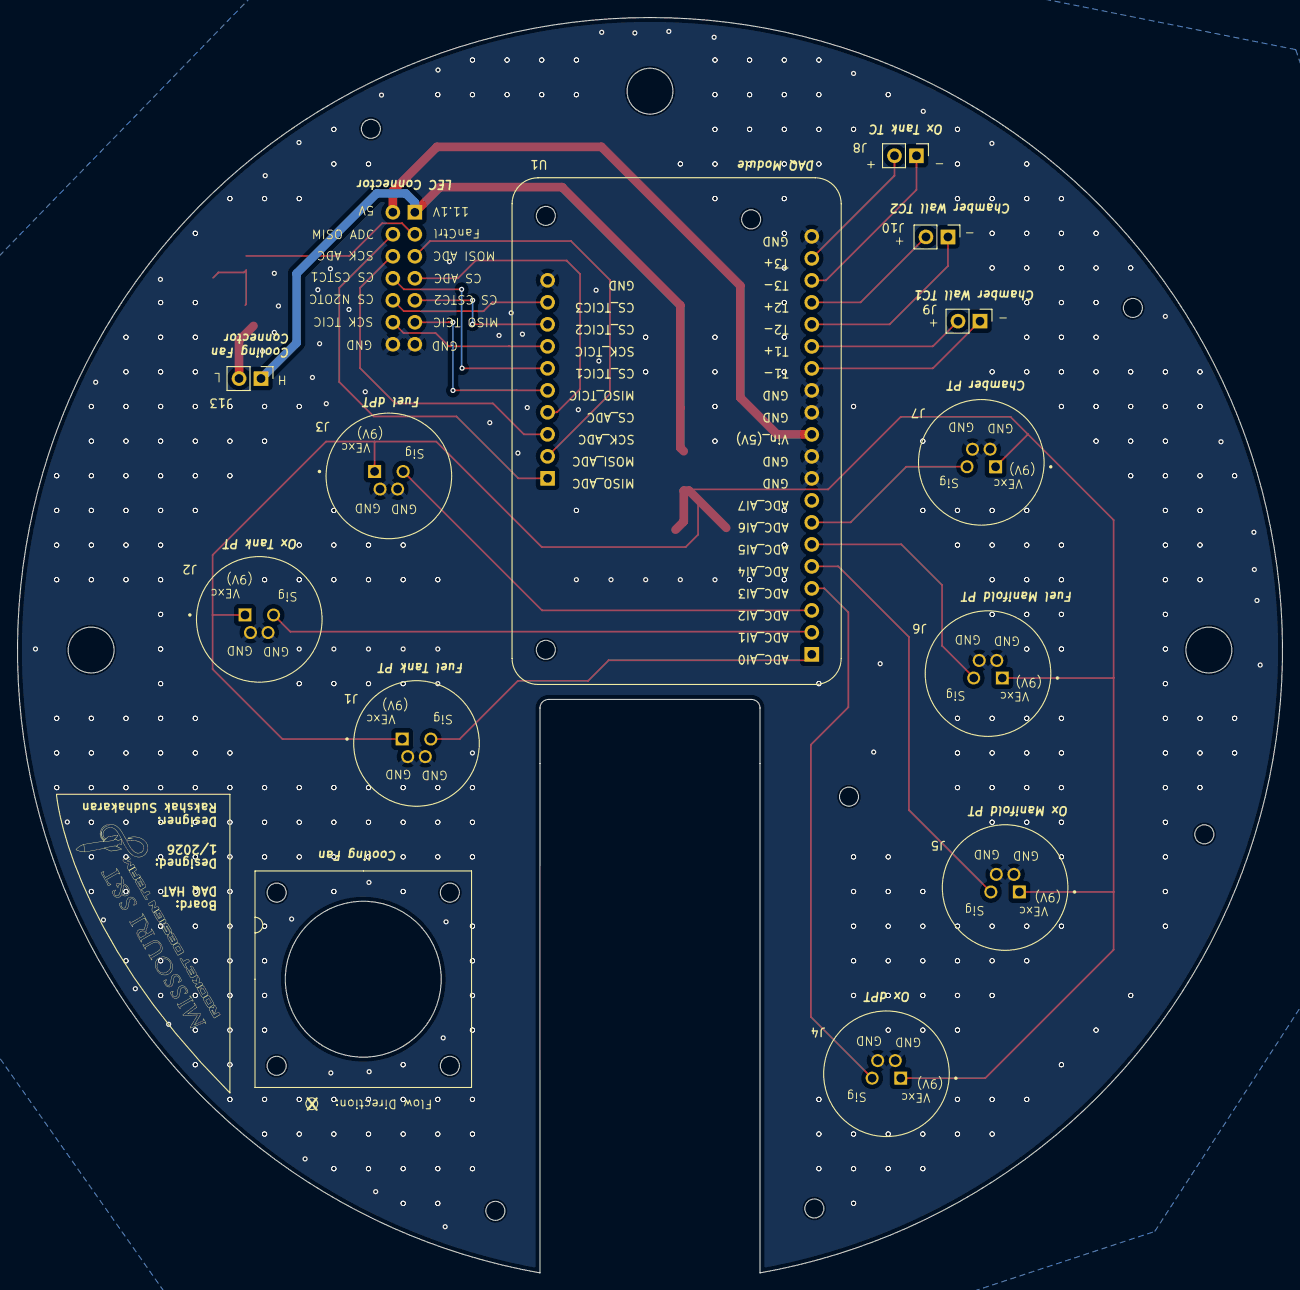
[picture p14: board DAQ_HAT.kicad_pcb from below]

Board: 2 copper layers, 146.0 x 144.9 mm, 20 parts (12 on the bottom side), 29 nets.

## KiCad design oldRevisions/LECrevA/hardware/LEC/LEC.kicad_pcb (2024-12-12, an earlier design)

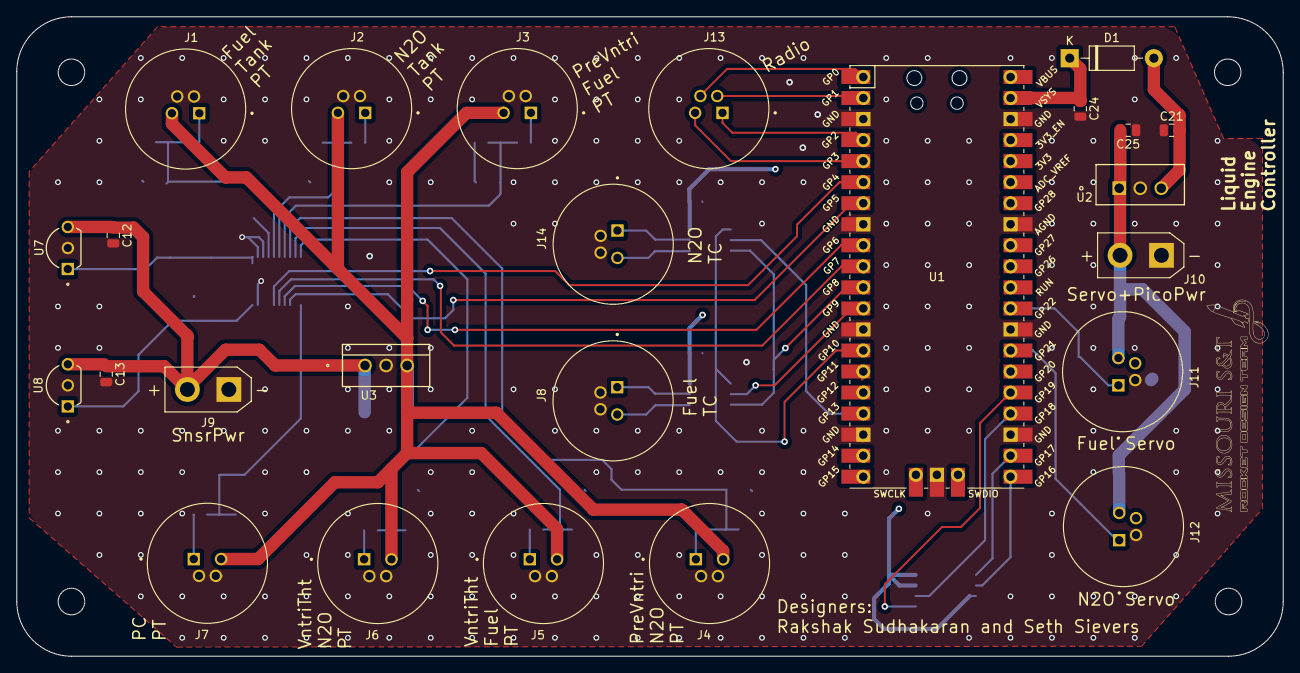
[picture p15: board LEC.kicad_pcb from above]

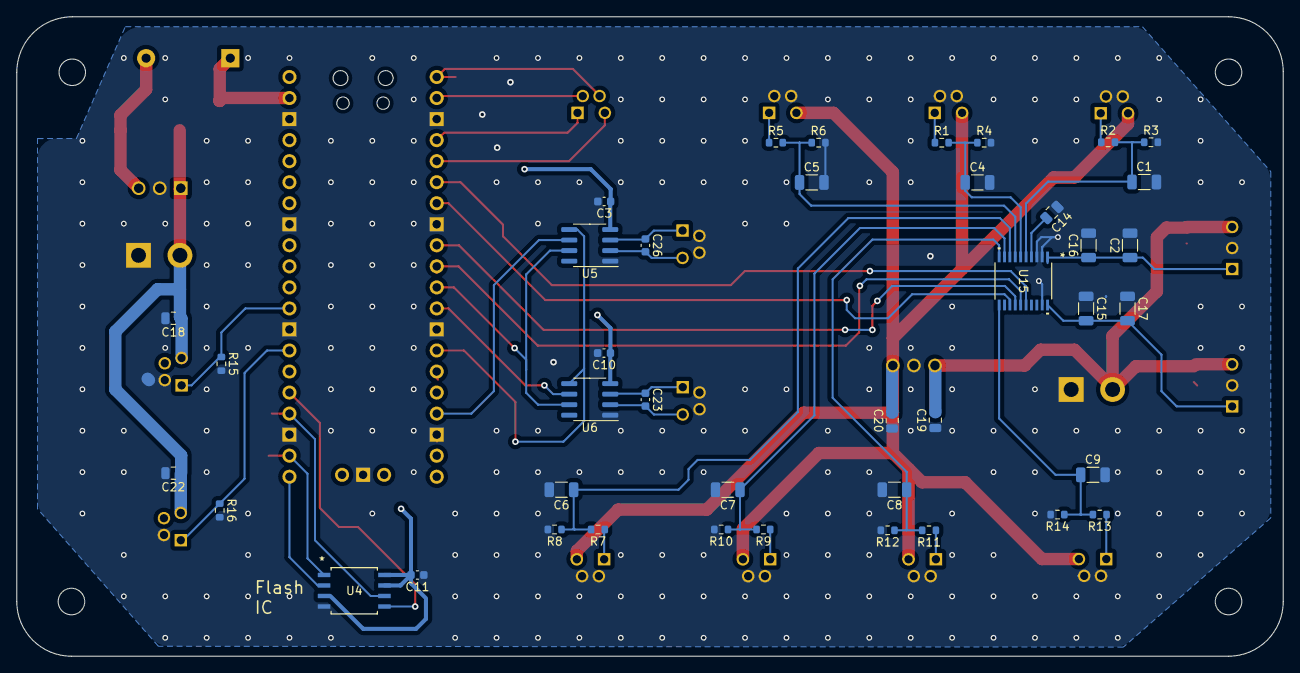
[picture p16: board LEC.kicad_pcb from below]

Board: 4 copper layers, 152.9 x 77.2 mm, 66 parts (41 on the bottom side), 46 nets.

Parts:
C1, C2, C4, C5, C6, C7, C8, C9, C15, C16, C17: 100n; C_1206_3216Metric
C3, C10, C11: 100n; C_0603_1608Metric
C12, C13, C14, C18, C19, C20, C21, C22, C24, C25: 10u; C_0805_2012Metric
C23, C26: 10n; C_0603_1608Metric
D1: 1N5817; D_DO-41_SOD81_P10.16mm_Horizontal
J1, J2, J3, J4, J5, J6, J7, J8, J11, J12, J13, J14: 54-00278; TENSILITY_54-00278
J9, J10: Conn_01x02; AMASS_XT30UPB-M_1x02_P5.0mm_Vertical
R1, R2, R3, R4, R5, R6, R7, R8, R9, R10, R11, R12, R13, R14, R15, R16: 10K; R_0603_1608Metric
U1: Pico; RPi_Pico_SMD_TH
U2: L7805; TO-220_STM
U3: MC7809CTG; TO-220AB_ONS
U4: W25Q128JVSIQ; SOIC_128JVSIQ_WIN
U5, U6: MAX31855KASA; SOIC-8_3.9x4.9mm_P1.27mm
U7, U8: L78L33ACZ; TO-92-TR_STM
U15: MCP3564RT-E/ST; TSSOP20_ST_MCH

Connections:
+3.3V: C3.1, C10.1, C11.2, U1.36 (3V3), U4.3 (WP_(IO2)), U4.7 (/HOLD_or_/RESET_(IO3)), U4.8 (VCC), U5.4 (V_CC), U6.4 (V_CC)
+12V: C18.1, C22.1, C25.2, J10.2, J11.3, J12.3, U2.1 (IN)
/ADC_Power_Circuit/AVDDOUT: C2.1, C16.1, U7.1 (VOUT), U15.1 (AVDD)
/ADC_Power_Circuit/DVDDOUT: C15.2, C17.2, U8.1 (VOUT), U15.20 (DVDD)
/ADC_Power_Circuit/VIN: C12.1, C13.1, C19.2, J9.2, U3.1 (INPUT), U7.3 (VIN), U8.3 (VIN)
/ExcIn: C20.2, J1.3, J2.3, J3.3, J4.3, J5.3, J6.3, J7.3, U3.3 (OUTPUT)
/GPIO0 (MISO): J13.4, U1.1 (GPIO0)
/GPIO1 (CS): J13.2, U1.2 (GPIO1)
/GPIO2 (SCK): J13.1, U1.4 (GPIO2)
/GPIO3 (MOSI): J13.3, U1.5 (GPIO3)
/GPIO4 (MISO): U1.6 (GPIO4), U15.16 (SDO)
/GPIO5 (CS): U1.7 (GPIO5), U15.13 (*CS)
/GPIO6 (SCK): U1.9 (GPIO6), U15.14 (SCK)
/GPIO7 (MOSI): U1.10 (GPIO7), U15.15 (SDI)
/GPIO8 (MISO): U1.11 (GPIO8), U5.7 (SO), U6.7 (SO)
/GPIO9 (CS): U1.12 (GPIO9), U6.6 (~CS)
/GPIO10 (SCK): U1.14 (GPIO10), U5.5 (SCK), U6.5 (SCK)
/GPIO13 (CS): U1.17 (GPIO13), U5.6 (~CS)
/GPIO16 (MISO): U1.21 (GPIO16), U4.2 (DO_(IO1))
/GPIO17 (CS): U1.22 (GPIO17), U4.1 (/CS)
/GPIO18 (SCK): U1.24 (GPIO18), U4.6 (CLK)
/GPIO19 (MOSI): U1.25 (GPIO19), U4.5 (DI_(IO0))
/Sig1: J1.1, R2.1
/Sig2: J2.1, R1.1
/Sig3: J3.1, R5.1
/Sig4: J4.1, R7.1
/Sig5: J5.1, R9.1
/Sig6: J6.1, R11.1
/Sig7: J7.1, R13.1
/lowPassFilter1/Sig_{out}: C4.1, R1.2, R4.1, U15.6 (CH1)
/lowPassFilter2/Sig_{out}: C5.1, R5.2, R6.1, U15.7 (CH2)
/lowPassFilter3/Sig_{out}: C6.1, R7.2, R8.1, U15.8 (CH3)
/lowPassFilter4/Sig_{out}: C7.1, R9.2, R10.1, U15.9 (CH4)
/lowPassFilter5/Sig_{out}: C8.1, R11.2, R12.1, U15.10 (CH5)
/lowPassFilter6/Sig_{out}: C9.1, R13.2, R14.1, U15.11 (CH6)
/lowPassFilter/Sig_{out}: C1.1, R2.2, R3.1, U15.5 (CH0)
GND: C1.2, C2.2, C3.2, C4.2, C5.2, C6.2, C7.2, C8.2, C9.2, C10.2, C11.1, C12.2, C13.2, C14.1, C15.1, C16.2, C17.1, C18.2, C19.1, C20.1, C21.1, C22.2, C24.2, C25.1, J1.2, J1.4, J2.2, J2.4, J3.2, J3.4, J4.2, J4.4, J5.2, J5.4, J6.2, J6.4, J7.2, J7.4, J8.2, J8.4, J9.1, J10.1, J11.2, J12.2, J14.2, J14.4, R3.2, R4.2, R6.2, R8.2, R10.2, R12.2, R14.2, R15.2, R16.2, U1.3 (GND), U1.8 (GND), U1.13 (GND), U1.18 (GND), U1.23 (GND), U1.28 (GND), U1.33 (AGND), U1.38 (GND), U1.42 (GND), U2.2 (GND), U3.2 (GROUND), U4.4 (GND), U5.1 (GND), U6.1 (GND), U7.2 (GND), U8.2 (GND), U15.2 (AGND), U15.3 (REFIN-), U15.19 (DGND)
unnamed: C21.2, D1.2 (A), U2.3 (OUT)
unnamed: C24.1, D1.1 (K), U1.39 (VSYS)
unnamed: J12.1, R16.1, U1.27 (GPIO21)
unnamed: J11.1, R15.1, U1.29 (GPIO22)
unnamed: C26.1, J14.1, U5.3 (T+)
unnamed: C26.2, J14.3, U5.2 (T-)
unnamed: C23.1, J8.1, U6.3 (T+)
unnamed: C23.2, J8.3, U6.2 (T-)
unnamed: C14.2, U15.4 (REFIN+/OUT)

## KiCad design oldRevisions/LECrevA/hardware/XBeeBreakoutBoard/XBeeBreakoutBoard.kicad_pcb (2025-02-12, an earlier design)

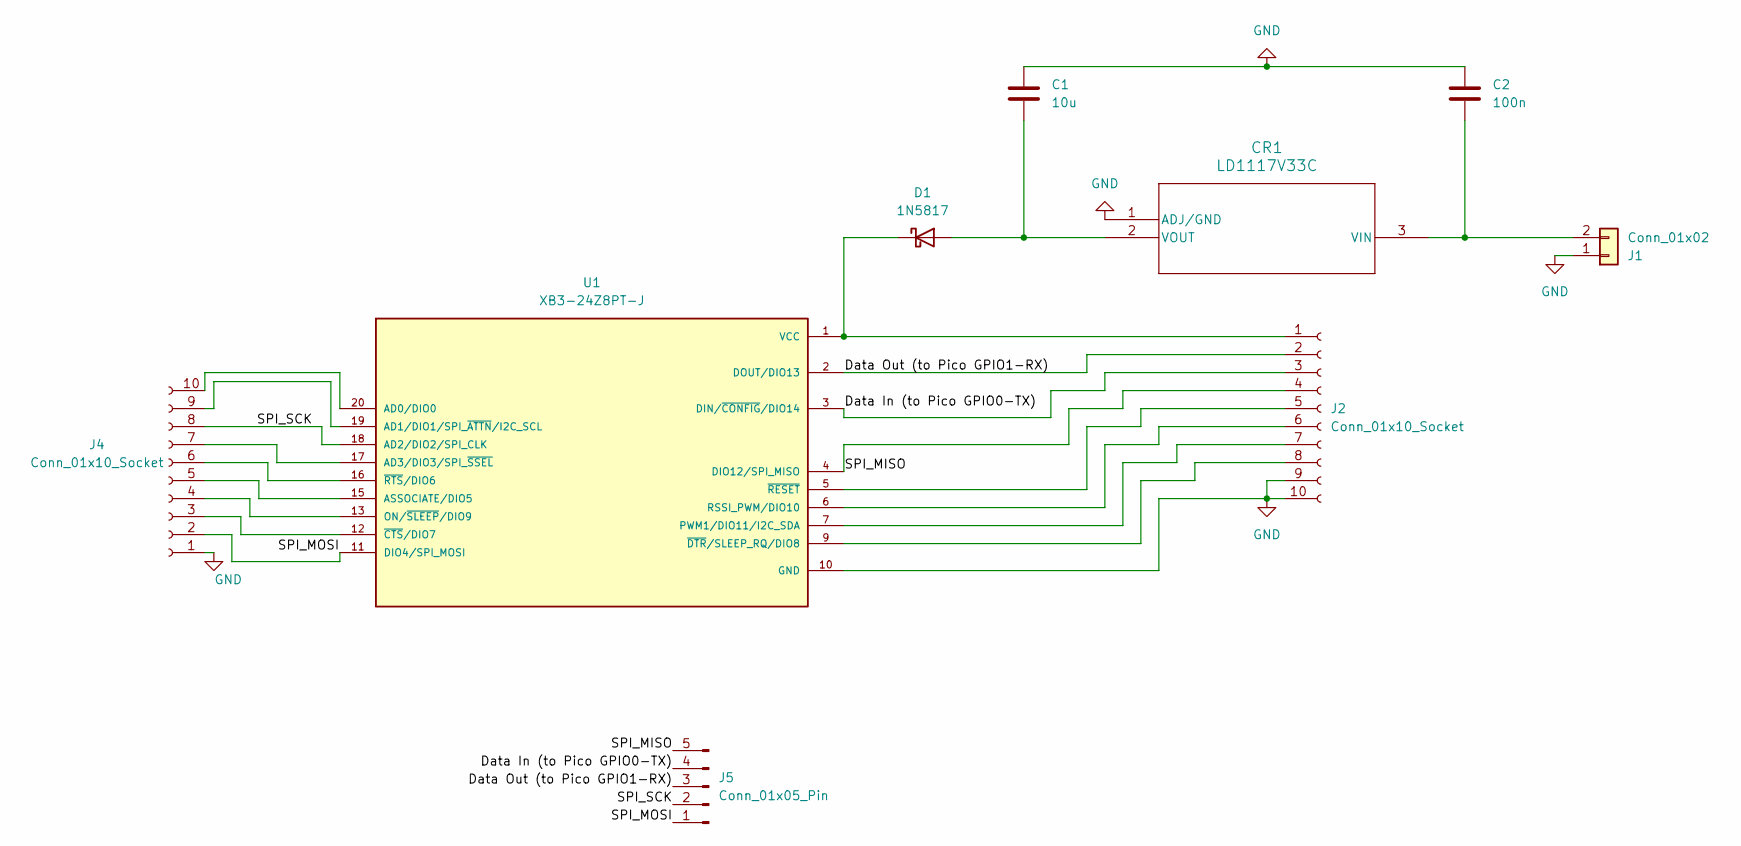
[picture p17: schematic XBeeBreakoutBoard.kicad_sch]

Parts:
C1: 10u; C_0805_2012Metric
C2: 100n; C_0603_1608Metric
CR1: LD1117V33C; TO-220_STM
D1: 1N5817; D_DO-41_SOD81_P10.16mm_Horizontal
J1: Conn_01x02; AMASS_XT30UPB-M_1x02_P5.0mm_Vertical
J2, J4: Conn_01x10_Socket; PinSocket_1x10_P2.54mm_Vertical
J5: Conn_01x05_Pin; PinSocket_1x05_P2.54mm_Vertical
U1: XB3-24Z8PT-J; XCVR_XB3-24Z8PT-J; PARTREV N/A

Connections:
/Data In (to Pico GPIO0-TX): J2.3, J5.4, U1.3 (DIN/~CONFIG/DIO14)
/Data Out (to Pico GPIO1-RX): J2.2, J5.3, U1.2 (DOUT/DIO13)
/SPI_MISO: J2.4, J5.5, U1.4 (DIO12/SPI_MISO)
/SPI_MOSI: J4.2, J5.1, U1.11 (DIO4/SPI_MOSI)
/SPI_SCK: J4.8, J5.2, U1.18 (AD2/DIO2/SPI_CLK)
GND: C1.1, C2.1, CR1.1 (ADJ/GND), J1.1, J2.9, J2.10, J4.1, U1.10 (GND)
unnamed: C2.2, CR1.3 (VIN), J1.2
unnamed: C1.2, CR1.2 (VOUT), D1.2 (A)
unnamed: D1.1 (K), J2.1, U1.1 (VCC)
unnamed: J2.5, U1.5 (~RESET)
unnamed: J2.6, U1.6 (RSSI_PWM/DIO10)
unnamed: J2.7, U1.7 (PWM1/DIO11/I2C_SDA)
unnamed: J2.8, U1.9 (~DTR/SLEEP_RQ/DIO8)
unnamed: J4.3, U1.12 (~CTS/DIO7)
unnamed: J4.4, U1.13 (ON/~SLEEP/DIO9)
unnamed: J4.5, U1.15 (ASSOCIATE/DIO5)
unnamed: J4.6, U1.16 (~RTS/DIO6)
unnamed: J4.7, U1.17 (AD3/DIO3/SPI_~SSEL)
unnamed: J4.9, U1.19 (AD1/DIO1/SPI_~ATTN/I2C_SCL)
unnamed: J4.10, U1.20 (AD0/DIO0)

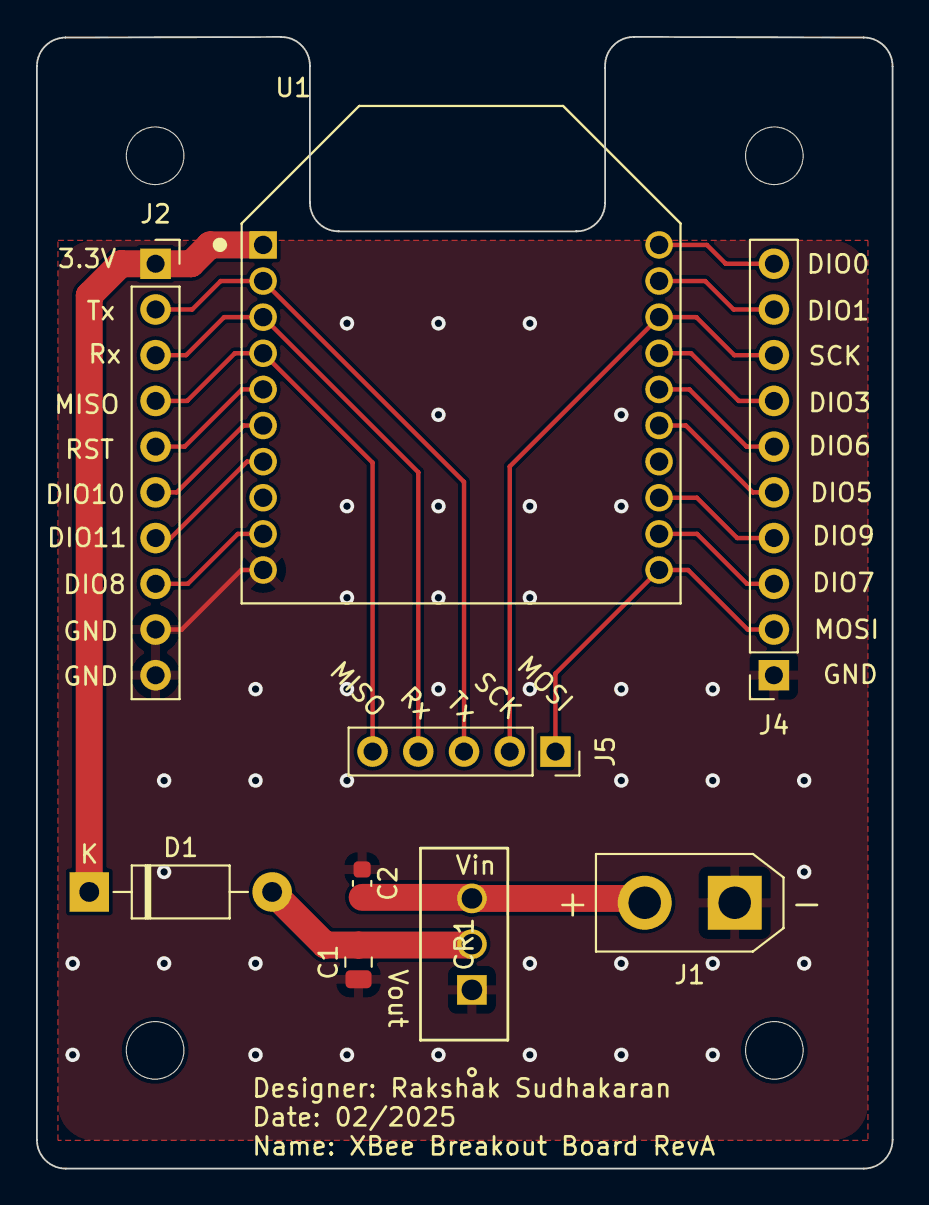
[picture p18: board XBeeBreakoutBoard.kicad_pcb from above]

Board: 2 copper layers, 47.5 x 62.9 mm, 9 parts (0 on the bottom side), 20 nets.

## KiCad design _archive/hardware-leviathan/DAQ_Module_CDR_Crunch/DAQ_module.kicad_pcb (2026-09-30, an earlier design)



Board: 4 copper layers, 38.0 x 58.5 mm, 52 parts (16 on the bottom side), 38 nets.

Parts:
C1, C3, C5, C6, C11, C17, C21, C22, C23, C24, C25, C26: 100n; C_0603_1608Metric
C2, C8, C19: 1u; C_0805_2012Metric
C4, C7, C13: 2.2u; C_1206_3216Metric
C9, C10, C20: 0.1u; C_0603_1608Metric
C12: 10u; C_0805_2012Metric
C14, C15, C16: 10n; C_0603_1608Metric
C18: 10u; C_1210_3225Metric
J1: Conn_01x10_Pin; PinHeader_1x10_P2.54mm_Vertical
J3: Conn_01x20_Pin; PinHeader_1x20_P2.54mm_Vertical
R1: 0.2; R_0603_1608Metric
R2, R3, R4, R5, R6, R7, R8, R9, R10, R11, R12, R13, R14, R15, R16, R17: 10K; R_0603_1608Metric
U1: MCP3564RT-E/ST; TSSOP20_ST_MCH
U2, U3, U8: MAX31855KASA; SOIC-8_3.9x4.9mm_P1.27mm
U5, U6, U7: TPS70933DBVR; DBV5_TEX

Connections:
+5V: C2.2, C8.1, C19.2, J3.11, U5.1 (IN), U6.1 (IN), U7.1 (IN)
/ADC_AI0: J3.1, R3.1
/ADC_AI1: J3.2, R4.1
/ADC_AI2: J3.3, R6.1
/ADC_AI3: J3.4, R8.1
/ADC_AI4: J3.5, R10.1
/ADC_AI5: J3.6, R12.1
/ADC_AI6: J3.7, R14.1
/ADC_AI7: J3.8, R16.1
/ADC_AI_Filt_0: C11.2, R2.1, R3.2, U1.5 (CH0)
/ADC_AI_Filt_1: C17.2, R4.2, R5.1, U1.6 (CH1)
/ADC_AI_Filt_2: C21.2, R6.2, R7.1, U1.7 (CH2)
/ADC_AI_Filt_3: C22.2, R8.2, R9.1, U1.8 (CH3)
/ADC_AI_Filt_4: C23.2, R10.2, R11.1, U1.9 (CH4)
/ADC_AI_Filt_5: C24.2, R12.2, R13.1, U1.10 (CH5)
/ADC_AI_Filt_6: C25.2, R14.2, R15.1, U1.11 (CH6)
/ADC_AI_Filt_7: C26.2, R16.2, R17.1, U1.12 (CH7)
/ADC_Power_Supply/AVDDOUT: C1.2, C3.2, C4.1, U1.1 (AVDD), U5.5 (OUT)
/ADC_Power_Supply/DVDDOUT: C5.1, C6.1, C7.1, R1.1, U1.20 (DVDD), U6.5 (OUT)
/GPIO4 (MISO_ADC): J1.1, U1.16 (SDO)
/GPIO5 (CS_ADC): J1.4, U1.13 (*CS)
/GPIO6 (SCK_ADC): J1.3, U1.14 (SCK)
/GPIO7 (MOSI_ADC): J1.2, U1.15 (SDI)
/GPIO8 (MISO_TCIC): J1.5, U2.7 (SO), U3.7 (SO), U8.7 (SO)
/GPIO9 (CS Chamber Shell_1): J1.6, U8.6 (~CS)
/GPIO10 (SCK_TCIC): J1.7, U2.5 (SCK), U3.5 (SCK), U8.5 (SCK)
/GPIO12 (CS_N20): J1.9, U3.6 (~CS)
/GPIO13 (CS Chamber Shell_2): J1.8, U2.6 (~CS)
/T+ (Chamber Shell_1): C14.1, J3.15, U8.3 (T+)
/T+ (Chamber Shell_2): C16.1, J3.17, U2.3 (T+)
/T+ (N2O): C15.1, J3.19, U3.3 (T+)
/T- (Chamber Shell_1): C14.2, J3.14, U8.2 (T-)
/T- (Chamber Shell_2): C16.2, J3.16, U2.2 (T-)
/T- (N2O): C15.2, J3.18, U3.2 (T-)
GND: C1.1, C2.1, C3.1, C4.2, C5.2, C6.2, C7.2, C8.2, C9.2, C10.2, C11.1, C12.1, C13.2, C17.1, C18.2, C19.1, C20.2, C21.1, C22.1, C23.1, C24.1, C25.1, C26.1, J1.10, J3.9, J3.10, J3.12, J3.13, J3.20, R2.2, R5.2, R7.2, R9.2, R11.2, R13.2, R15.2, R17.2, U1.2 (AGND), U1.3 (REFIN-), U1.19 (DGND), U2.1 (GND), U3.1 (GND), U5.2 (GND), U6.2 (GND), U7.2 (GND), U8.1 (GND)
unnamed: C18.1, R1.2
unnamed: C12.2, U1.4 (REFIN+/OUT)
unnamed: C9.1, C10.1, C13.1, C20.1, U2.4 (V_{CC}), U3.4 (V_{CC}), U7.5 (OUT), U8.4 (V_{CC})

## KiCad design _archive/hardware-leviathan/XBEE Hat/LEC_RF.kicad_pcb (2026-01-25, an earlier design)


Board: 2 copper layers, 60.0 x 40.0 mm, 11 parts (0 on the bottom side), 6 nets.

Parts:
C1: 22uF; C_0805_2012Metric
C2: 10u; C_1210_3225Metric
C3: 10uF; C_0805_2012Metric
C4, C5, C6: 100n; C_0603_1608Metric
C10: 1u; C_0805_2012Metric
CR1: LD1086DT33TR; TO-252-2
FB1: FerriteBead; R_0603_1608Metric
J2: Conn_01x04; PinHeader_1x04_P2.54mm_Vertical
U1: XBP9X-DMUS-001; XBEE_GND_PAD

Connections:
+5V: C5.2, FB1.1, J2.4
+5V_Filt: C3.1, C6.2, CR1.3 (INPUT), FB1.2
/UART_RX: J2.3, U1.4 (DIO14/UART_RX/~CONFIG)
/UART_TX: J2.2, U1.3 (DIO13/UART_TX)
GND: C1.2, C2.2, C3.2, C4.1, C5.1, C6.1, C10.2, CR1.1 (ADJ/GND), J2.1, U1.1 (GND), U1.11 (GND), U1.13 (GND), U1.22 (GND), U1.35 (GND), U1.38 (GND)
VCC: C1.1, C2.1, C4.2, C10.1, CR1.2 (OUTPUT), U1.2 (VCC)

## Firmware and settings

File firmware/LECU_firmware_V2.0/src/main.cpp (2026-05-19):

#include <Arduino.h>
#include <Servo.h>
#include <control.h>
#include <RPi_Pico_TimerInterrupt.h>
#include <DAQ.h>
#include <Adafruit_SPIFlash.h>
#include <SdFat.h>
#define FLASH_CS   17
#define FLASH_SCK  18
#define FLASH_MISO 16
#define FLASH_MOSI 19
#define flashSPI SPI


// Pin Assignments
int indicatorLEDPin = 22;
int fuelMainValvePWMPin   = 26;
int oxMainValvePWMPin     = 27;
int LECUServoPwrSwitchPin = 28;
int fanCtrlPin = 14;
Servo fuelValve;
Servo oxValve;

// -------------------- Control States --------------------
// Loop-owned states
char LECUServoPwrSwitchState;
char N2OMainValvePurgeState;
char mainValvesState;
char throttlingAlgorithmState;

static unsigned long lastLEDMillis = 0;
static unsigned long currentLEDMillis = 0;
static int LEDState = LOW;

// ------------------- Sensor Data -----------------------
volatile uint32_t AI0Reading;
volatile uint32_t AI1Reading;
volatile uint32_t AI2Reading;
volatile uint32_t AI3Reading;
volatile uint32_t AI4Reading;
volatile uint32_t AI5Reading;
volatile uint32_t AI6Reading;
volatile uint32_t TC1Reading;
volatile uint32_t TC2Reading;
volatile uint32_t TC3Reading;

// ------------------- Flash IC ------------------------
Adafruit_FlashTransport_SPI flashTransport(
    FLASH_CS,
    flashSPI
);
Adafruit_SPIFlash flash(&flashTransport);

typedef struct __attribute__((packed)) {

    uint32_t timestamp_ms;
    uint32_t AI0;
    uint32_t AI1;
    uint32_t AI2;
    uint32_t AI3;
    uint32_t AI4;
    uint32_t AI5;
    uint32_t AI6;
    uint32_t TC1;
    uint32_t TC2;
    uint32_t TC3;

} SensorLogRecord;

uint32_t flashWriteAddress = 0;


// -------------------- Serial RX --------------------
const byte NUM_CHARS = 4;
char receivedChars[NUM_CHARS];
bool newData = false;

// -------------------- Timer --------------------
RPI_PICO_Timer ITimer0(0);
const int SENSOR_DATA_TX_INTERVAL = 200;   // in ms
volatile bool sendDataFlag = false;
volatile bool logDataFlag = false;
volatile uint32_t tick = 0;

// -------------------- Function Declarations --------------------
void recv_with_start_end_markers();
void process_ctrl_packet();
void send_sensor_data();
void log_sensor_data_to_flash();
bool send_sensor_data_ISR(struct repeating_timer *t);


void setup() {
  Serial1.begin(115200);
  //Serial.begin(115200);
  pinMode(LECUServoPwrSwitchPin, OUTPUT);
  pinMode(indicatorLEDPin, OUTPUT);
  pinMode(LED_BUILTIN, OUTPUT);
  pinMode(fanCtrlPin, OUTPUT);
  digitalWrite(fanCtrlPin, HIGH);

  fuelValve.attach(fuelMainValvePWMPin, 500, 2500);
  oxValve.attach(oxMainValvePWMPin, 500, 2500);

  init_DAQ();
  delay(1500);

  flashSPI.setRX(FLASH_MISO);
  flashSPI.setTX(FLASH_MOSI);
  flashSPI.setSCK(FLASH_SCK);
  flashSPI.begin();

  SPI.begin();

  if (!flash.begin()) {
    digitalWrite(LED_BUILTIN, HIGH);
    while (1) {
      delay(100);
    }
  }
  

  // Timer ISR every 10 ms
  ITimer0.attachInterruptInterval(SENSOR_DATA_TX_INTERVAL*1000, send_sensor_data_ISR);
}

void loop() {
  recv_with_start_end_markers();
  if (newData) {
    process_ctrl_packet();
    newData = false;
  }

  if (sendDataFlag) {
    sendDataFlag = false;
    read_DAQ_module(AI0Reading, AI1Reading, AI2Reading, AI3Reading, AI4Reading, AI5Reading, AI6Reading, TC1Reading, TC2Reading, TC3Reading);
    send_sensor_data();
  }

  if (logDataFlag) {
    logDataFlag = false;
    log_sensor_data_to_flash();
  }

  currentLEDMillis = millis();

  if ( ((LECUServoPwrSwitchState == 'L') || (LECUServoPwrSwitchState == 'H')) ) {
    if ((currentLEDMillis - lastLEDMillis) >= 1000) {
      lastLEDMillis = currentLEDMillis;
      LEDState = (LEDState == LOW) ? HIGH : LOW;
      digitalWrite(indicatorLEDPin, LEDState);
    }
  } else {
    digitalWrite(indicatorLEDPin, LOW);
  }
  
}


void recv_with_start_end_markers() {
  static boolean recvInProgress = false;
  static byte ndx = 0;
  char startMarker = '<';
  char endMarker = '>';
  char rc;

  while (Serial1.available() > 0 && newData == false) {
    rc = Serial1.read();

    if (recvInProgress == true) {
      if (rc != endMarker) {
        receivedChars[ndx] = rc;
        ndx++;
        if (ndx >= NUM_CHARS) {
          ndx = NUM_CHARS - 1;
        }
      } else {
        recvInProgress = false;
        ndx = 0;
        newData = true;
      }
    } else if (rc == startMarker) {
      recvInProgress = true;
    }
  }
}

void process_ctrl_packet() {

  // ---- Critical section: copy shared RX buffer ----
  noInterrupts();
  LECUServoPwrSwitchState = receivedChars[0];
  N2OMainValvePurgeState        = receivedChars[1];
  mainValvesState        = receivedChars[2];
  throttlingAlgorithmState  = receivedChars[3];
  interrupts();

  // ---- Update hardware (interrupts ENABLED) ----
  update_onboard_states(
    LECUServoPwrSwitchState,
    N2OMainValvePurgeState,
    mainValvesState,
    throttlingAlgorithmState,
    LECUServoPwrSwitchPin,
    oxValve,
    fuelValve,
    indicatorLEDPin
  );
}

void send_sensor_data() {

  uint8_t packet[42];

  packet[0] = '<';

  uint32_t values[10] = {
    AI0Reading,
    AI1Reading,
    AI2Reading,
    AI3Reading,
    AI4Reading,
    AI5Reading,
    AI6Reading,
    TC1Reading,
    TC2Reading,
    TC3Reading
  };

  memcpy(&packet[1], values, sizeof(values));

  packet[41] = '>';

  Serial1.write(packet, sizeof(packet));
}

void log_sensor_data_to_flash() {

    SensorLogRecord record;

    record.timestamp_ms = tick;
    record.AI0 = AI0Reading;
    record.AI1 = AI1Reading;
    record.AI2 = AI2Reading;
    record.AI3 = AI3Reading;
    record.AI4 = AI4Reading;
    record.AI5 = AI5Reading;
    record.AI6 = AI6Reading;
    record.TC1 = TC1Reading;
    record.TC2 = TC2Reading;
    record.TC3 = TC3Reading;

    // Erase 4KB sector when entering new sector
    if ((flashWriteAddress % 4096) == 0) {
      flash.eraseSector(flashWriteAddress);
    }

    flash.writeBuffer(
        flashWriteAddress,
        (uint8_t*)&record,
        sizeof(record)
    );

    flashWriteAddress += sizeof(record);
}

bool send_sensor_data_ISR(struct repeating_timer *t) {
  tick++;
  sendDataFlag = true;  // Set flag only
  if (tick % 5 == 0) {
    logDataFlag = true;
  }
  return true;
}

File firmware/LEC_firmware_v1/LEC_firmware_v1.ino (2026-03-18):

#include <Serial.h>
#include <Servo.h>

#define XBee Serial1

//::::::::::::::: LEC(End Device) ::::::::::::::::::::::::::

Servo fuelServo; //Initialize fuel servo object
Servo oxServo; //Initialize ox servo object

const int FUEL_PWM_PIN = 26; //Attach fuel servo to GPIO 22 (pin 10)
const int OX_PWM_PIN = 27; //Attach ox servo to GPIO 21 (pin 14)

const int OX_OPEN_ANGLE = 1000; //Define the pulse width that means "open"
const int OX_CLOSE_ANGLE = 2500; //Define the pulse width that means "close"
const int FUEL_OPEN_ANGLE = 1000;
const int FUEL_CLOSE_ANGLE = 2500;

const byte txHeader[] = {0x7E, 0x00, 0x0E, 0x10, 0x01, 0x00, 0x13, 0xA2, 0x00, 0x42, 0x54, 0x0B, 0xE6, 0xFF, 0xFE, 0x00, 0x00};
const byte msgTermChar[] = {0x00, 0x00, 0x00, 0x3E};

// Radio Message Parsing Variable  for (int i = 0; i < 4; i++){
    XBee.print(msgTermChar[i]);
  }s
bool parsed = true;
char incomingByte;
char msg[24];
int idx = 0;

// Throttling algo placeholder
bool tAlgoEnable = false;

void setup() {
  // Initialize Serial0 (USB), and Serial1 (XBEE UART)
  XBee.begin(115200);

  // Set servo power pin
  pinMode(28, OUTPUT); 

  // Peripherial init
  pinMode(LED_BUILTIN, OUTPUT);
  digitalWrite(LED_BUILTIN, LOW);
  fuelServo.attach(FUEL_PWM_PIN, FUEL_CLOSE_ANGLE, FUEL_OPEN_ANGLE);
  oxServo.attach(OX_PWM_PIN, OX_OPEN_ANGLE, OX_CLOSE_ANGLE);
}

void XBeeRx() {
  while (XBee.available() > 0) {
    incomingByte = XBee.read();
    msg[idx] = incomingByte;

    idx++;
    parsed = false;
  }
}

void XBeeTxNoise(){
  for (int i = 0; i < 17; i++){
    XBee.print(txHeader[i]);
  }

  for (int i = 0; i < 4; i++){
    XBee.print(msgTermChar[i]);
  }

  for (int j = 0; j < 52; j++){
    XBee.print((byte)random(256));
  }

  for (int i = 0; i < 4; i++){
    XBee.print(msgTermChar[i]);
  }

  XBee.print(0); // Dummy checksum
}

void Parse(){
  // Check that it's an RX packet 
  if (msg[3] == 0x90){
    // For all cmds, default to "safe state" if any command other than the high state is received
    if (msg[16] == 'H'){
      digitalWrite(28, HIGH);
    } else {
      digitalWrite(28, LOW);
    }

    if (msg[17] == 'O'){
      oxServo.writeMicroseconds(OX_OPEN_ANGLE);
    } else {
      oxServo.writeMicroseconds(OX_CLOSE_ANGLE);
    }

    if (msg[18] == 'O'){
      digitalWrite(LED_BUILTIN, HIGH);
      fuelServo.writeMicroseconds(FUEL_OPEN_ANGLE);
      oxServo.writeMicroseconds(OX_OPEN_ANGLE);
    }
    else{
      digitalWrite(LED_BUILTIN, LOW);
      fuelServo.writeMicroseconds(FUEL_CLOSE_ANGLE);
      oxServo.writeMicroseconds(OX_CLOSE_ANGLE);
    }
    
    tAlgoEnable = (msg[19] == 'T');
  }

  parsed = true;
  idx = 0;
}

void loop() {
  XBeeRx();
  
  // Only parse new unparsed data
  if (!parsed)
  {
    Parse();
  }

  XBeeTxNoise();

  delay(500)
}

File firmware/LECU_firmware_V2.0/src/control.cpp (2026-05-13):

#include <Arduino.h>
#include <Servo.h>
#include <control.h>

// Purpose: update onboard control hardware states (valve positions, indicator LED states, etc.) based on ctrlString index values. 
// Pre: 
// Post: 
void update_onboard_states(char LECUServoPwrSwitchState, char N2OMainPurgeState, char mainValvesState, char throttlingAlgorithmState,
                            int LECUServoPwrSwitchPin, Servo &oxValve, Servo &fuelValve, int indicatorLEDPin) {
    if (LECUServoPwrSwitchState == 'L') {
        digitalWrite(LECUServoPwrSwitchPin, LOW);
    } else if (LECUServoPwrSwitchState == 'H') {
        digitalWrite(LECUServoPwrSwitchPin, HIGH);
    }

    if (mainValvesState == 'O') {
        // Main valves override everything
        oxValve.writeMicroseconds(SERVO_OPEN_ANGLE_US);
        fuelValve.writeMicroseconds(SERVO_OPEN_ANGLE_US);
    } else if (mainValvesState == 'C') {
        // Fuel always follows main valves
        fuelValve.writeMicroseconds(SERVO_CLOSE_ANGLE_US);

        // Ox valve can still be controlled by purge
        if (N2OMainPurgeState == 'O') {
            oxValve.writeMicroseconds(SERVO_OPEN_ANGLE_US);
        } else if (N2OMainPurgeState == 'C') {
            oxValve.writeMicroseconds(SERVO_CLOSE_ANGLE_US);
        }
    }
    
    
    

}

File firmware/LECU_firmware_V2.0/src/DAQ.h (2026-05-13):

#ifndef DAQ_H
#define DAQ_H

#include <Arduino.h>
#include <SPI.h>
#include "MCP3x6x_Type_Definitions.h"                     // Variable definitions header-file.
#include "MCP3x6x_ADC_Definitions.h"                      // ADC definitions header-file.
#include "MCP3x6x_Peripheral_Definitions.h"               // Peripheral definitions header-file.
#include "MCP3x6x_SPI_Definitions.h"                      // SPI definitions header-file.


// -------------------------
// Pin Assignments
// -------------------------
extern int MCP3564_CS_PIN;
extern int TC1_CS_PIN;
extern int TC2_CS_PIN;
extern int TC3_CS_PIN;

// -------------------------
// Initialization
// -------------------------
void init_DAQ();

// -------------------------
// High‑level DAQ read function
// -------------------------
void read_DAQ_module(
    volatile uint32_t &AI0Reading,
    volatile uint32_t &AI1Reading,
    volatile uint32_t &AI2Reading,
    volatile uint32_t &AI3Reading,
    volatile uint32_t &AI4Reading,
    volatile uint32_t &AI5Reading,
    volatile uint32_t &AI6Reading,
    volatile uint32_t &TC1Reading,
    volatile uint32_t &TC2Reading,
    volatile uint32_t &TC3Reading
);

#endif

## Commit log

2024-10-19 Initial commit of LEC KiCad files
    [LEC.kicad_pcb, LEC.kicad_sch]
2024-11-09 Added LPFs and updated power circuits. Tidied up a bit
    [ADC_Power_Circuit.kicad_sch, LEC.kicad_sch, lowPassFilter.kicad_sch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]
2024-11-13 Updated LVR selection and other optimizations. Need to update footprints and symbols
    [ADC_Power_Circuit.kicad_sch, LEC.kicad_sch, lowPassFilter.kicad_sch]
2024-11-13 Removed resistors on ADC power lines
    [ADC_Power_Circuit.kicad_sch]
2024-11-16 Updated wiring of flash chip, connected 3V3 net, and added PWM pulldowns
    [LEC.kicad_sch]
2024-11-17 Added bulk capacitors to ADC LVRs, servos, and pico power inputs
    [ADC_Power_Circuit.kicad_sch, LEC.kicad_sch]
2024-11-22 Schematic done
    [ADC_Power_Circuit.kicad_sch, LEC.kicad_sch]
2024-11-23 Added decoupling capacitor across thermocouple inputs
    [LEC.kicad_sch]
2024-11-29 Initial commit of PCB files, updated schematic syntax to smooth PCB design workflow. Need to fill ground planes and other necessary updates
    [LEC.kicad_pcb, LEC.kicad_sch, lowPassFilter.kicad_sch]
2024-12-03 Added mounting holes, ground planes, and via stiching
    [LEC.kicad_pcb]
2024-12-03 Added labeling, moved ADC decoupling caps closer to ADC
    [LEC.kicad_pcb]
2024-12-09 Updated pin mapping of radio connector for cleaner routing
    [LEC.kicad_pcb, LEC.kicad_sch]
2024-12-12 Final updates
    [LEC.kicad_pcb]
2024-12-12 Added production files
    [LEC-B_Cu.gbl, LEC-B_Mask.gbs, LEC-B_Paste.gbp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]
2024-12-12 Updated schematic documentation, more production files
    [ADC_Power_Circuit.kicad_sch, LEC.csv, LEC.kicad_pcb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]
2025-01-20 added adc example
2025-02-08 Initial commit of XBee Breakout Board
    [XBeeBreakoutBoard.kicad_pcb, XBeeBreakoutBoard.kicad_sch]
2025-02-12 XBee Breakout production files
    [XBeeBreakoutBoard-B_Cu.gbl, XBeeBreakoutBoard-B_Mask.gbs, XBeeBreakoutBoard-B_Paste.gbp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]
2025-06-21 First commit of 25-26 design cycle. Structure update
    [ADC_Power_Circuit.kicad_sch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]
2025-10-03 Added XBEE module schematic and pcb
    [LEC_RF.kicad_pcb, LEC_RF.kicad_sch]
2025-10-04 DAQ Module
    [ADC_Power_Supply.kicad_sch, DAQ module.kicad_pcb, DAQ module.kicad_sch]
2025-10-08 Added full KiCad project for RF module
2025-10-10 Push of most recent schematic and PCB
    [LEC_RF.kicad_pcb, LEC_RF.kicad_sch]
2025-10-13 LECMainBoard initial commit. Ready for schematic review
    [ADC_Power_Supply.kicad_sch, Buck_Converter.kicad_sch, DAQ module.kicad_pcb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]
2025-10-13 Reverted to previous commit to undo any accidental changes
    [ADC_Power_Supply.kicad_sch, DAQ module.kicad_pcb]
2025-10-13 Added name to schematic
    [Buck_Converter.kicad_sch, LECV2.0_Main_Board.kicad_sch]
2025-10-16 Temp commit to upload changes to buck converter circuit
    [Buck_Converter.kicad_sch, LECV2.0_Main_Board.kicad_pcb, LECV2.0_Main_Board.kicad_sch]
2025-10-19 Implemented fixes. Ready for 2nd review
    [LECV2.0_Main_Board.kicad_sch]
2025-10-19 Routed XBEE PCB
    [LEC_RF.kicad_pcb, LEC_RF.kicad_sch]
2025-10-25 Intermediate commit, need to fix servo connector footprints
    [Buck_Converter.kicad_sch, LECV2.0_Main_Board.kicad_pcb, LECV2.0_Main_Board.kicad_sch]
2025-10-25 Fixed all footprints. Defined PCB edge, arbitrarily placed components
    [LECV2.0_Main_Board.kicad_pcb, LECV2.0_Main_Board.kicad_sch]
2025-10-27 Initial commit of DAQ_module revision to meet deadlines
    [ADC_Power_Supply.kicad_sch, DAQ_module.kicad_pcb, DAQ_module.kicad_sch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]
2025-10-27 Added GPIO clamping diodes, sufficient buck output capacitance, UVLO divider, and 3V3_EN diode
    [Buck_Converter.kicad_sch, LECV2.0_Main_Board.kicad_pcb, LECV2.0_Main_Board.kicad_sch]
2025-10-29 Ready for final review. Added downloadable footprint and symbol of board
    [ADC_Power_Supply.kicad_sch, DAQ_module.kicad_pcb, DAQ_module.kicad_sch]
2025-10-29 Fixed logo and mounting holes
    [DAQ_module.kicad_pcb]
2025-10-29 Improved some via spacing
    [DAQ_module.kicad_pcb]
2025-10-30 Added fix for downloadable footprint of DAQ Module CDR Crunch for 3rd mounting hole
2025-10-30 Fixed footprint and symbol input conn pinout to reflect schematic and PCB
2025-10-31 Final revision of XBEE board
    [LEC_RF.kicad_pcb, LEC_RF.kicad_sch]
2025-11-07 Added part numbers and datasheets
    [LEC_RF.kicad_sch]
2025-11-08 Fixed some traces' layer selection
    [DAQ_module.kicad_pcb]
2025-11-15 Experimenting with alternate layout bc no SMA connector
    [LEC_RF.kicad_pcb]
2025-11-15 Updated silkscreen text
    [DAQ_module.kicad_pcb]
2025-11-15 Routed revised XBEE PCB layout
    [LEC_RF.kicad_pcb]
2026-01-25 Finished PCBs
    [Buck_Converter.kicad_sch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]
2026-03-07 Basic servo test firmware for LEC flow-test
    [ADC_Power_Supply.kicad_sch, DAQ module.kicad_pcb, DAQ module.kicad_sch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]
2026-05-13 DAQ works fine, the GSEC Pico doesn't seem to be processing it correctly. No latency in comms
    [control.cpp, main.cpp]
2026-05-19 Added Flash IC functionality and cooling fan usage
